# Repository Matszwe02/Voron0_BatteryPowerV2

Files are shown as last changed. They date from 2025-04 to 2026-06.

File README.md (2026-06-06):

# Battery Power mod V2 for VORON 0


> [v1 version](https://github.com/Matszwe02/Voron0_BatteryPower)

### **Make your voron even more reliable and more portable**

This mod allows you to run your voron up to 1h with batteries. It's also a great UPS for it.

The original PSU stays inside, so you can plug in to C14 socket

## Features

- original PSU for on-grid powering
- 6x 21700 battery
- CC/CV charging the battery with PSU
- button to power on and power off (gracefully) with power indicator

## Print settings

- Voron recommended settings, so 4 walls, print with ABS
- Apply ABS shrinkage, the part is going through the whole printer width so 1mm off will make it not fit

## Custom circuit required
Circuit for switching on and off battery and disconnecting galvanically PSU when powered down
- see `Schematic.pdf`

## Parts required
- Original PSU
- 6x 21700 battery
- cc/cv buck converter
    - set to 23V (or any voltage you want to idle at) and around 1-2A
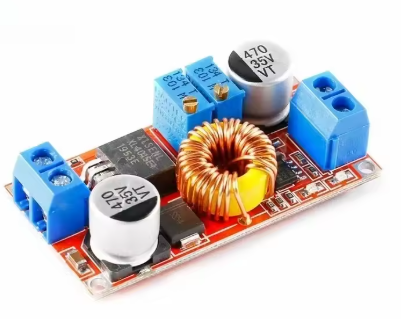
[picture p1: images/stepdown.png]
  > 
- boost converter
    - set to 24V (main power for printer)
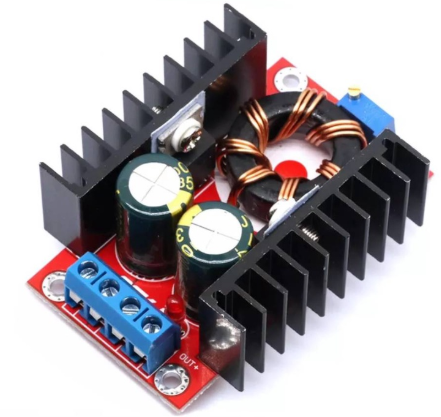
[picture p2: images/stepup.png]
  > 
- mosfet module
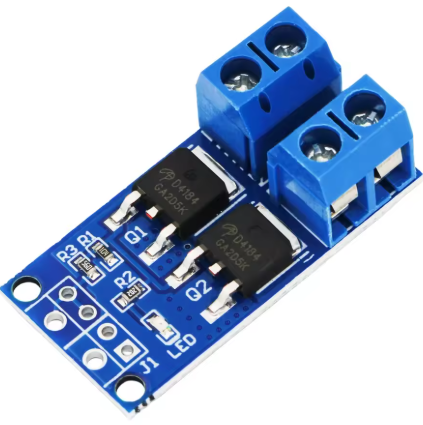
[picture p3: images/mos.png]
  > 
- 6s BMS
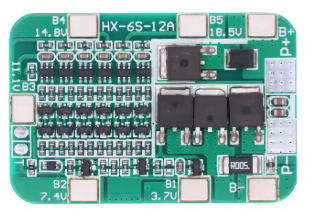
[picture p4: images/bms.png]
    > 
- C14 socket
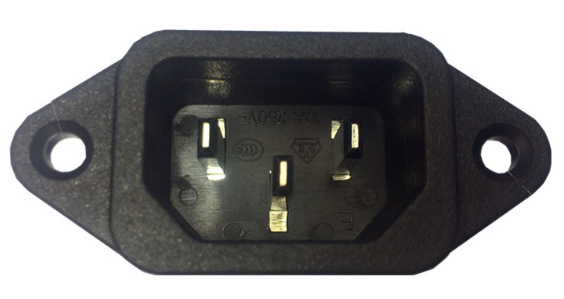
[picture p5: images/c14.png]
  > 
- DPST relay
    - 29x12.7x15.7mm
    - input 24V, output 8A/250V
- A few high power schottky diodes
    - recommended SBX2040 40V 20A
- Push switch of your choose, with LED indicator
- One red 3mm LED to inform printer is not AC powered
- components for custom PCB (see schematic)
- A few wire connectors (like WAGO)
- A bunch of high power and low power wires
- A bunch of heatset inserts and m3 screws (mostly 6/8/10mm)

## How to assemble
As per schematic.

**!! CAUTION there will be much work with high-power and high-voltage power lines, you must be absolutely sure of what you're doing !!**

- mains line goes through DPST relay (both L and N should be switchable) and to the psu
- 24V section is very tricky, take your time understanding what'g going where. Before connecting anything of that to mainboard or rpi, measure with multimeter how it works at idle, how it works when you apply voltage to power_good pin, how it responds to power button, etc. It's extra tricky, as there are 2 separate grounds and signals goind between them. One wrong step and 24V can be applied to rpi (however there are transoptors to minimise this risk). Good luck!
- step down needs to be screwed in first, with its connectors, as well as relay soldered and glued into place, then you can screw everything together (except skirts). The whole build has around 1mm of margin (in each direction), so keep that in mind. Watch out for the parts sitting on 1515 extrusions, as they're not all the same. Use the CAD as a guide.

## Installation

- Ensure your shutdown button is at GPIO 26 and pulled up
- Copy `PowerOff` to your home directory
- Run `install.sh`
- modify `main.py` if printer data is other than `~/printer_data`

## Images

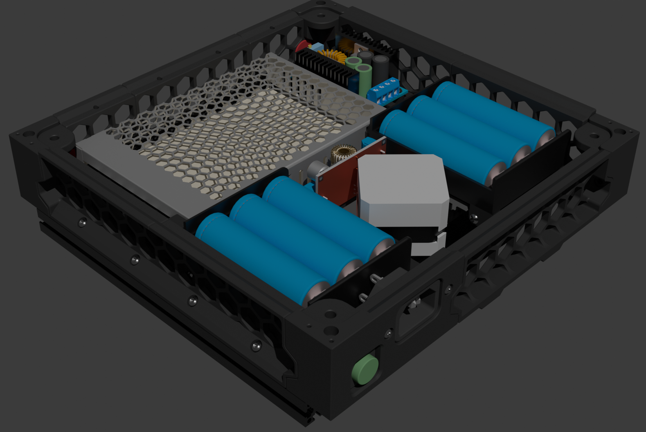
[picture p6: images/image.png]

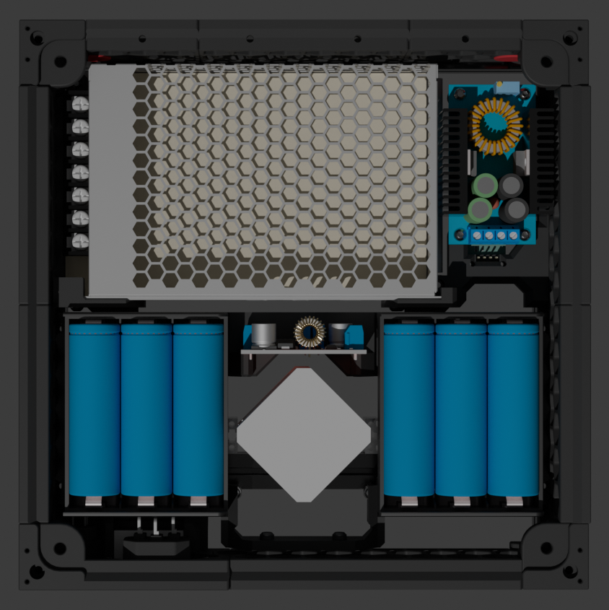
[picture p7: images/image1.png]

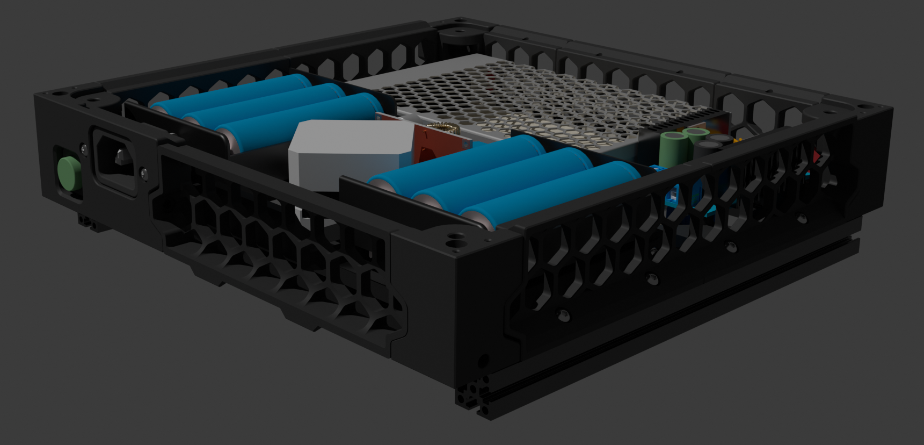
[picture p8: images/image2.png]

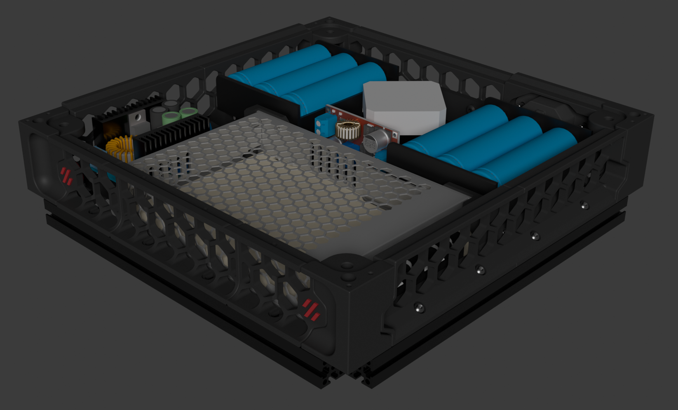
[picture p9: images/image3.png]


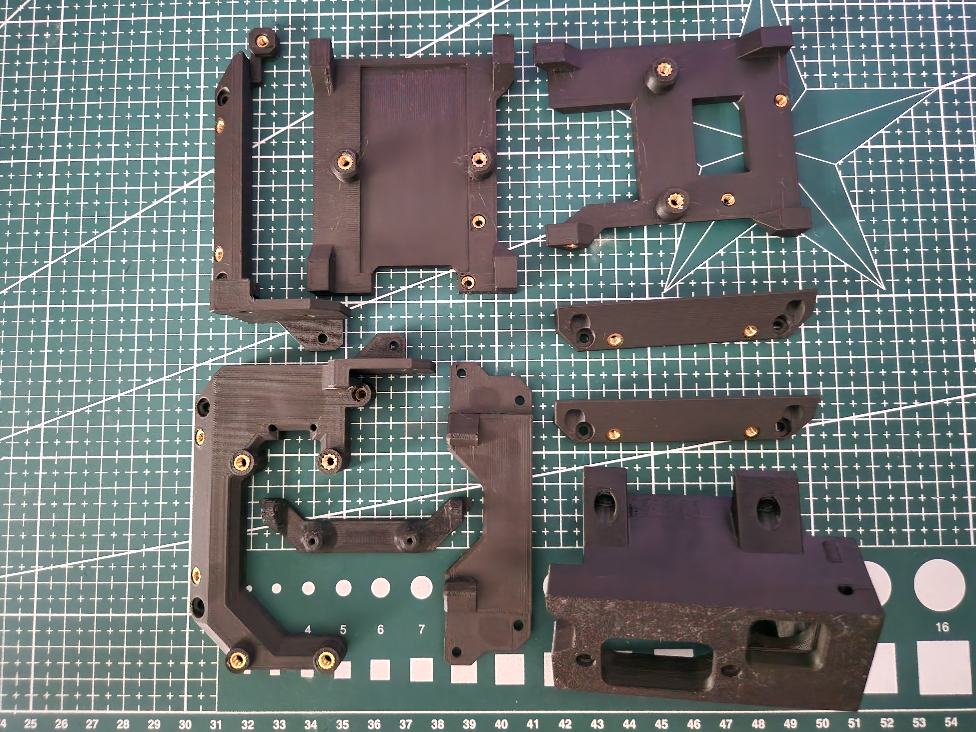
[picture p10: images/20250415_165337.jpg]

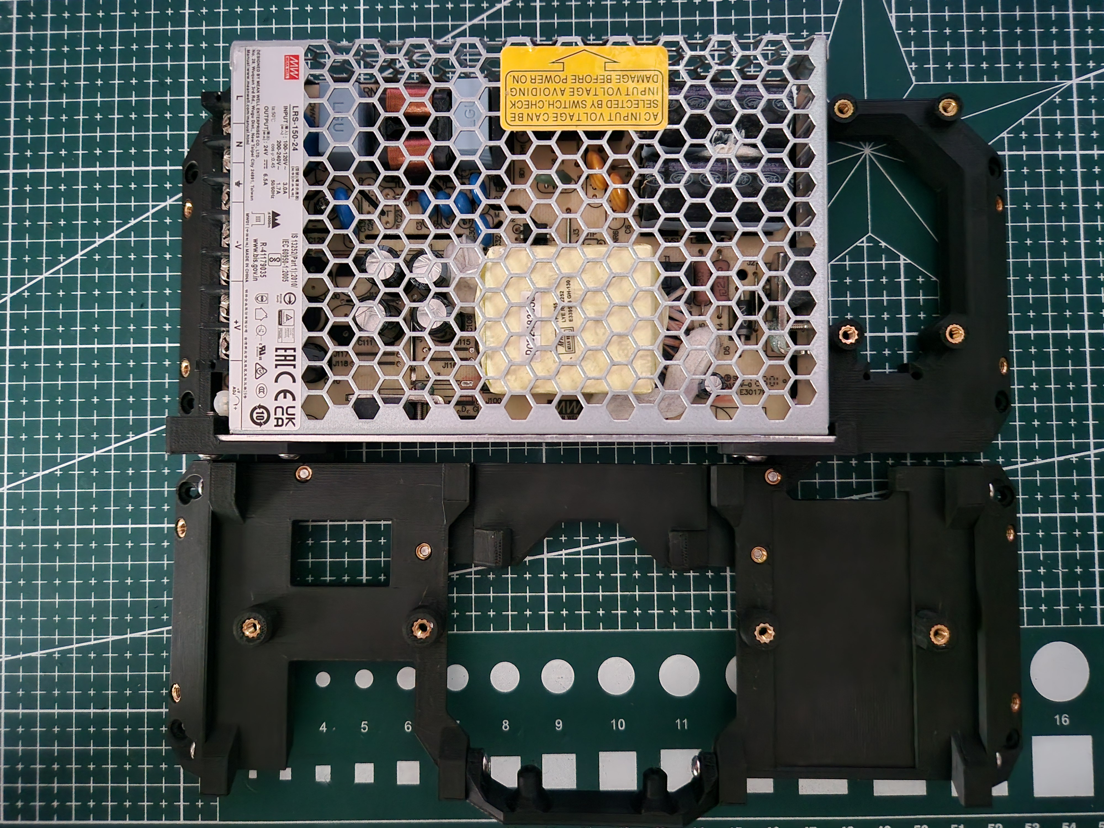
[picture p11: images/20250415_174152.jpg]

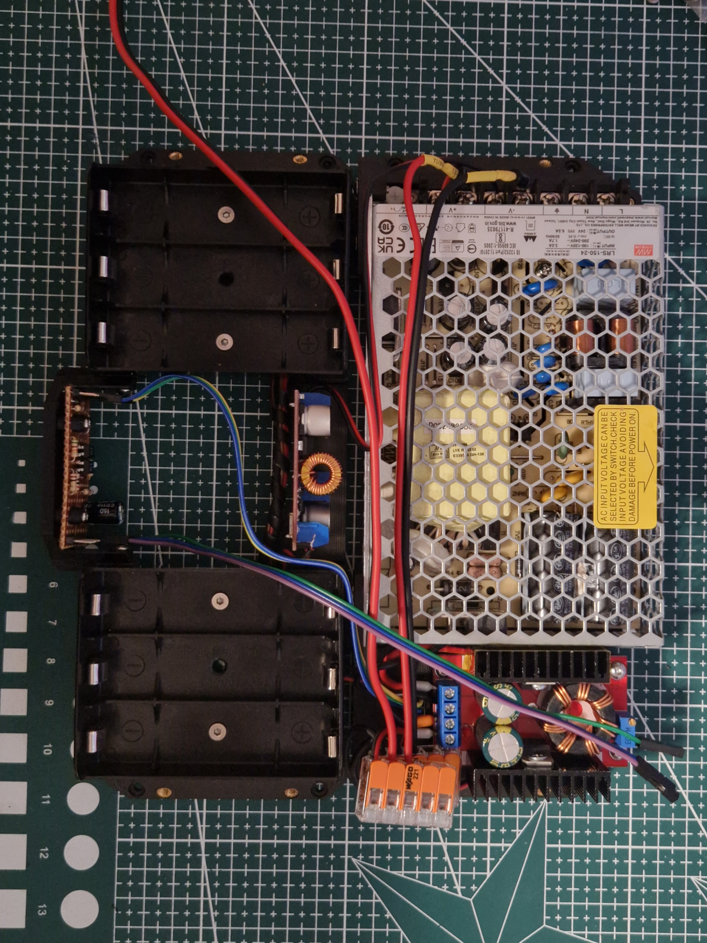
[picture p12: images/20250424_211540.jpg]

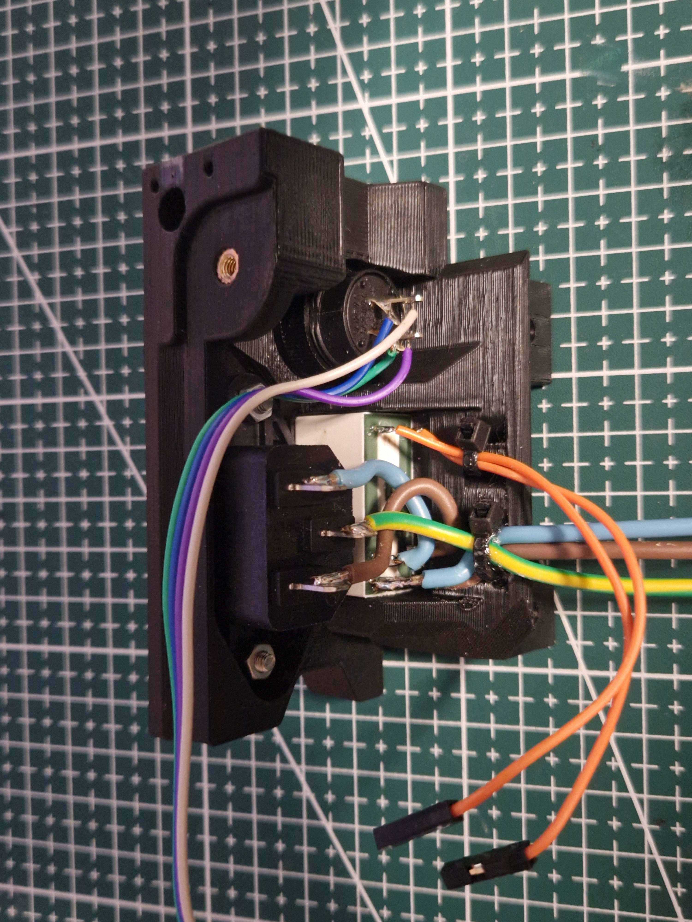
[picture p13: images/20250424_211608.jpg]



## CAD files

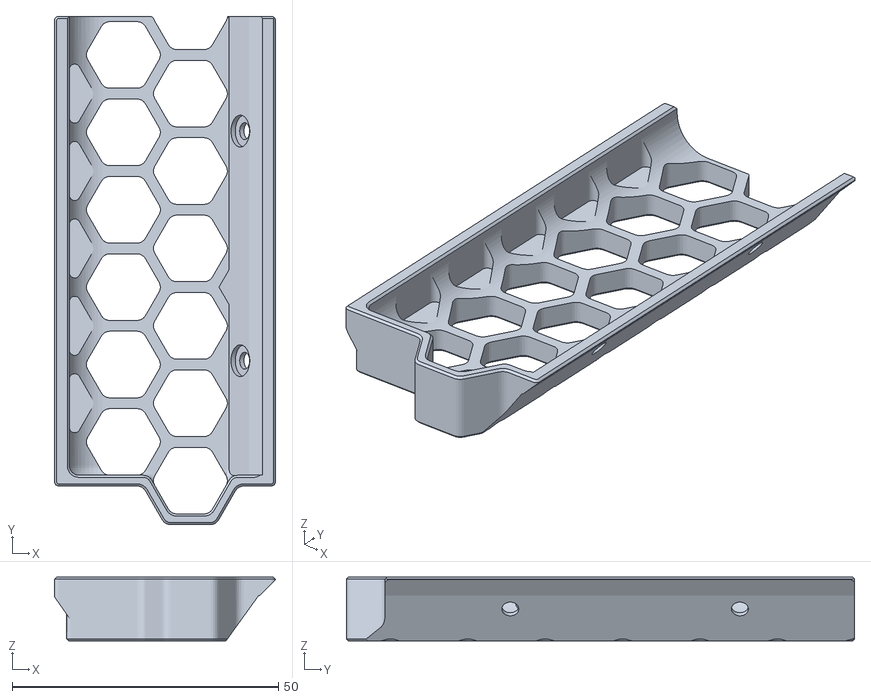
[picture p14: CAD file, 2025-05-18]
STL/Side_Skirt_Left_B_x1 (1) (1).stl.stl
41.5 x 95.5 x 12.0

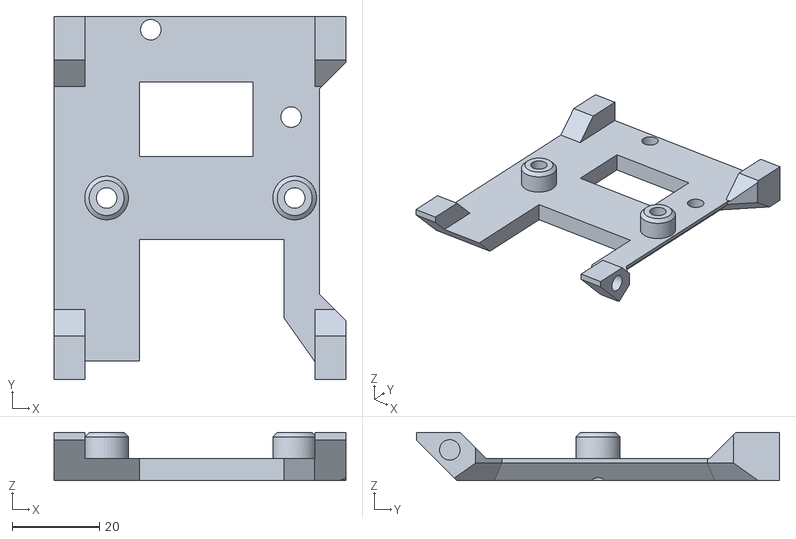
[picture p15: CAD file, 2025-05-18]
STL/Body24.stl.stl
66.7 x 83.0 x 11.0

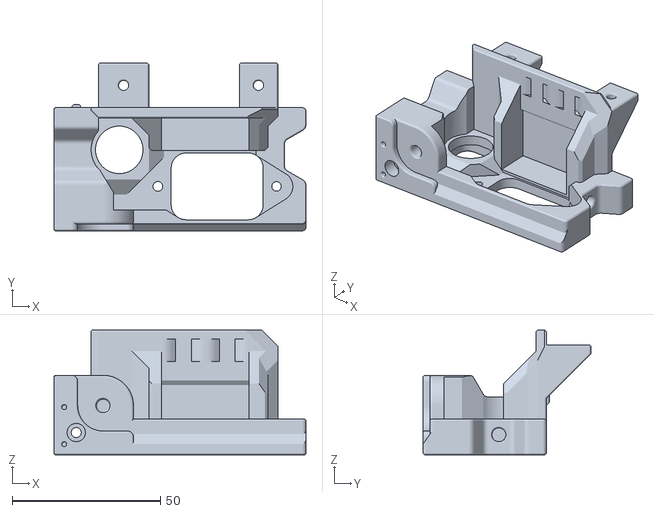
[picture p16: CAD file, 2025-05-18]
STL/Body7.stl.stl
84.9 x 56.5 x 42.0

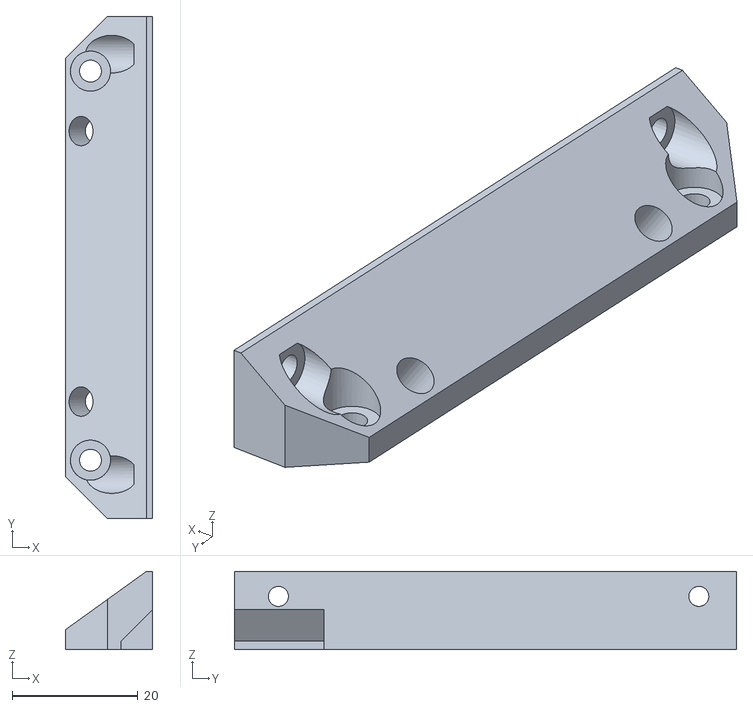
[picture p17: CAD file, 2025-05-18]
STL/Body19.stl.stl
13.9 x 80.0 x 12.5

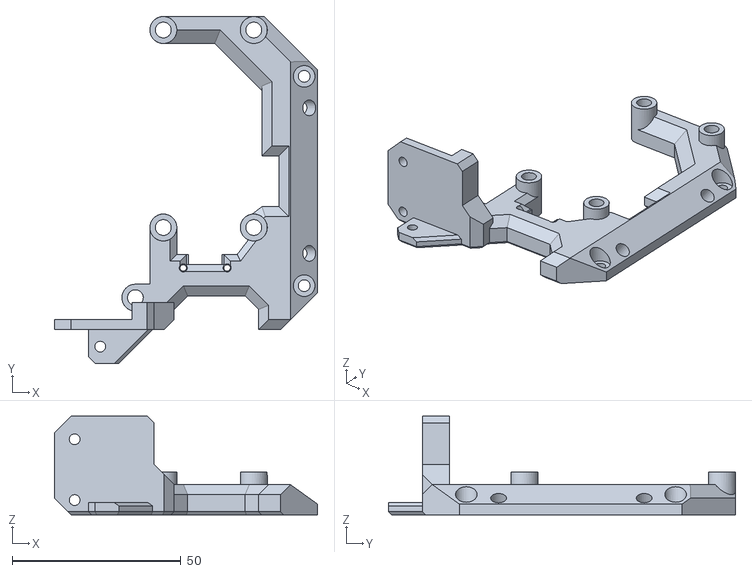
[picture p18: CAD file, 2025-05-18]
STL/Body2.stl.stl
78.0 x 102.8 x 29.3

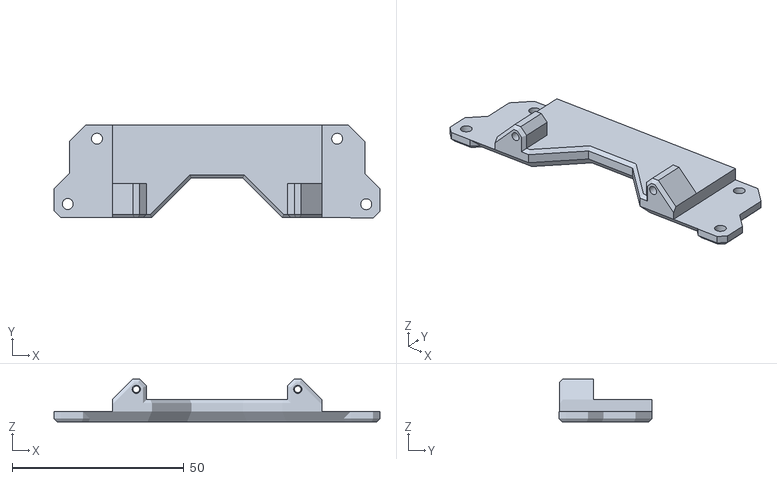
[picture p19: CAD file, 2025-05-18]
STL/Body21.stl.stl
94.9 x 27.1 x 12.5

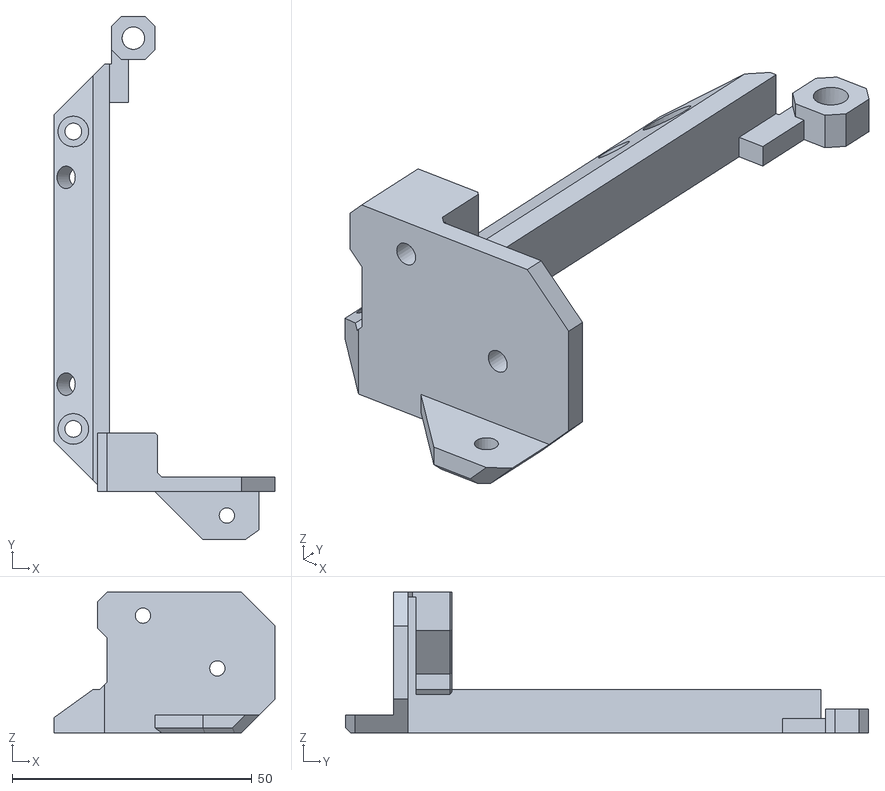
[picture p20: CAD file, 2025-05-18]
STL/Body4.stl.stl
46.0 x 109.0 x 29.3

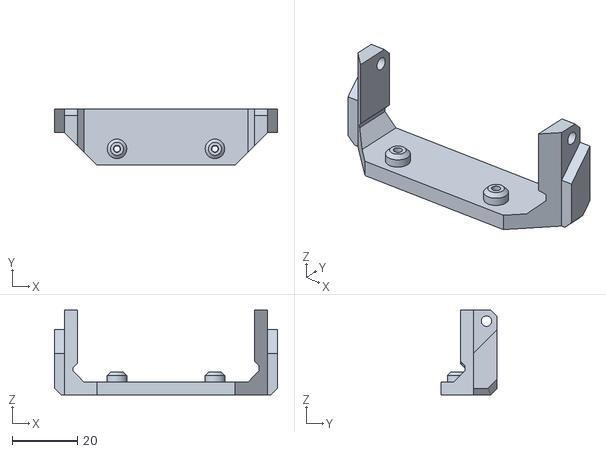
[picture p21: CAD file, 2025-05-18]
STL/Body25.stl.stl
68.3 x 17.3 x 26.0

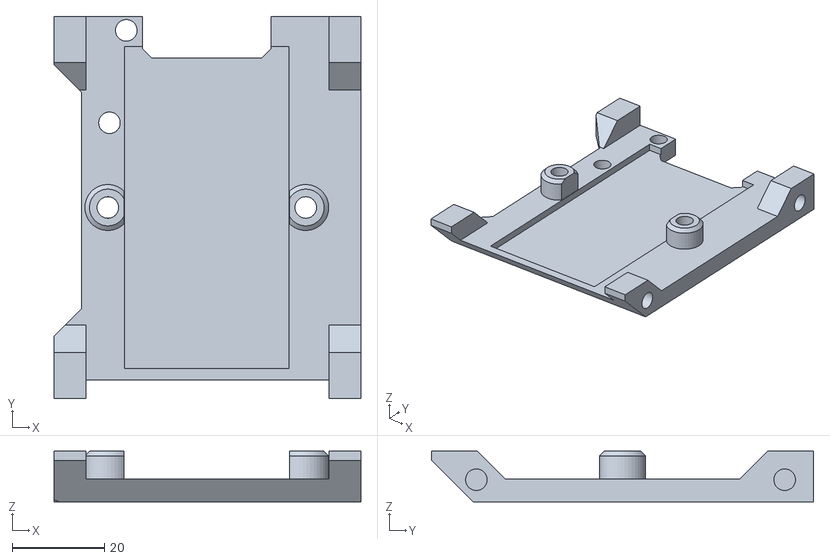
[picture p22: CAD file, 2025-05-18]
STL/Body17.stl.stl
66.7 x 83.0 x 11.0

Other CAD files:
STL/Body23.stl.stl
STL/Side_Skirt_Left_B_x1 (1) (1).stl(3).stl
STL/Side_Skirt_Left_B_x1 (1) (1).stl(1).stl
STL/Side_Skirt_Left_B_x1 (1) (1).stl(2).stl

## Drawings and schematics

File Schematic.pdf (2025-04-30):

## RPI

## MOSFET MODULE

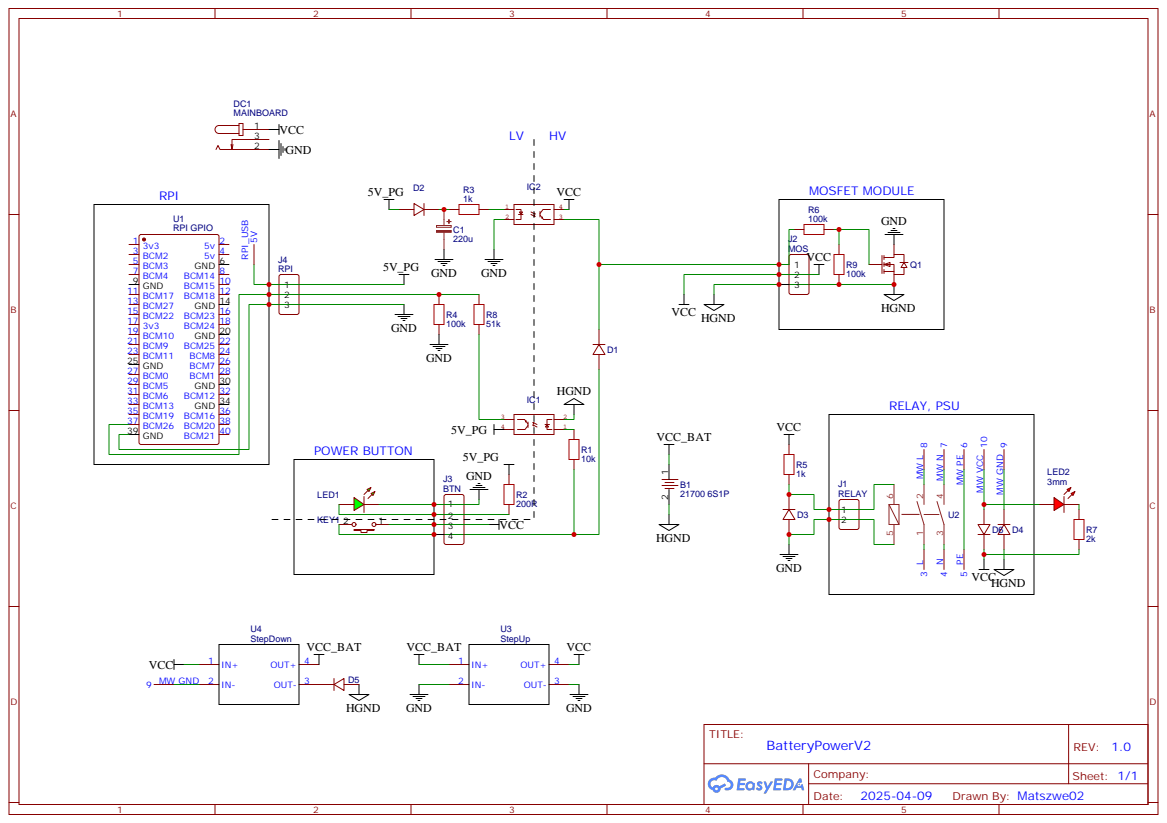
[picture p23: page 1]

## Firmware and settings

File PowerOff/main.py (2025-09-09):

import RPi.GPIO as gpio
from time import sleep
import os
import subprocess

SHUTDOWN_PIN = 26

home = os.path.expanduser('~')
gcode_console = os.path.join(home, 'printer_data', 'comms', 'klippy.serial')


def run_gcode(command):
    with open(gcode_console, 'a') as console:
        console.write(command + '\n')

def shutdown_printer(channel):
    for _ in range(50):
        if gpio.input(SHUTDOWN_PIN) == gpio.HIGH:
            return
        sleep(0.01)
    run_gcode("_SHUTDOWN")
    sleep(120)
    subprocess.run(["shutdown", "-h", "now"])
    subprocess.run(["sudo", "shutdown", "-h", "now"])
    sleep(120)


gpio.setmode(gpio.BCM)
gpio.setup(SHUTDOWN_PIN, gpio.IN)

sleep(1)

gpio.add_event_detect(SHUTDOWN_PIN, gpio.FALLING)
gpio.add_event_callback(SHUTDOWN_PIN, shutdown_printer)

while True:
    sleep(60)
    if gpio.input(SHUTDOWN_PIN) == gpio.LOW:
        shutdown_printer()

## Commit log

2025-04-25 Add PowerOff script
2025-04-30 Upload schematic
2025-05-18 Add CAD
    [Body17.stl.stl, Body19.stl.stl, Body2.stl.stl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]
2025-09-09 Fix: Improve shutdown reliability and user home directory resolution
    [main.py]
2025-09-09 Fix: shutdown pin logic
    [main.py]
